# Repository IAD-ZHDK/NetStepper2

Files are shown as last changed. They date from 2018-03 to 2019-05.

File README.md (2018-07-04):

# NetStepper2
A networked stepper motor controller based on the ESP-WROOM-32 and the L6470. Examples built with netStepper can be seen in this [video](https://vimeo.com/278343342).  
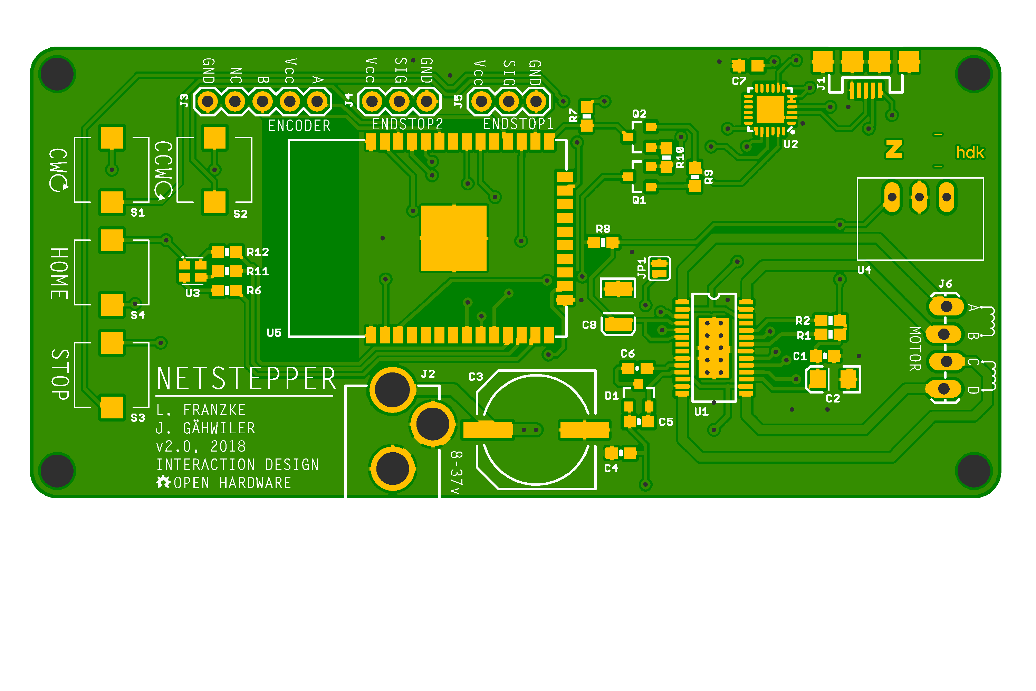
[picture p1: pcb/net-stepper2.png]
Board

## Parts

### Controllers

- Stepper Controller: `L6470` ([Datasheet](https://www.mouser.com/ds/2/389/l6470-954753.pdf), [Mouser](https://www.mouser.ch/ProductDetail/STMicroelectronics/L6470H?qs=sGAEpiMZZMuP%2fQeRSdvksPGSQkvtk%2fGb))
- SoC: `ESP-WROOM-32` ([Datasheet](https://espressif.com/sites/default/files/documentation/esp-wroom-32_datasheet_en.pdf), [Mouser](https://www.mouser.ch/ProductDetail/Adafruit/3320?qs=%2fha2pyFaduhvAZY8Ie1SD0odCwfSxZwX5aiqddL%252ba6k%3d))
- USB/UART: `CP2104` ([Datasheet](https://www.mouser.com/ds/2/368/cp2104-37496.pdf), [Mouser](https://www.mouser.ch/ProductDetail/Silicon-Labs/CP2104-F03-GMR?qs=sGAEpiMZZMtXqW1IUNX6MBk8lKhQ2c4Y))

### Interface

- RGB LED: `CLMVB-FKA-CFHEHLCBB7a363` ([Datasheet](https://www.mouser.com/ds/2/90/CLMVBFKA-276021.pdf), [Mouser](https://www.mouser.ch/ProductDetail/Cree-Inc/CLMVB-FKA-CFHEHLCBB7a363/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))
- Micro USB: `ZX62-B-5PA(33)` ([Datasheet](https://www.mouser.com/ds/2/185/ZX_catalog-939768.pdf), [Mouser](https://www.mouser.ch/ProductDetail/Hirose-Connector/ZX62-B-5PA33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))

### Other

- NPN Transistor: `MMBT2222` ([Datasheet](https://www.mouser.com/ds/2/308/MMBT2222LT1-D-80103.pdf), [Mouser](https://www.mouser.ch/ProductDetail/863-SMMBT2222ALT3G?r=863-SMMBT2222ALT3G))
- Double Diodes: `BAV99` ([Datasheet](https://www.mouser.com/ds/2/308/BAV99-1118535.pdf), [Mouser](https://www.mouser.ch/ProductDetail/ON-Semiconductor-Fairchild/BAV99?qs=sGAEpiMZZMudZehw8RjeZe6BnmRwGdH1))
- Traco: `TSR 1-2433`: ([Datasheet](https://www.mouser.com/ds/2/687/tsr1-537631.pdf), [Mouser](https://www.mouser.ch/ProductDetail/TRACO-Power/TSR-1-2433?qs=sGAEpiMZZMsF1ODjcwEocIuESINJH25XntreftV5zWI%3d))
- Button: `B3AL1002P-MS`: ([Datasheet](https://www.mouser.com/ds/2/307/en-b3al-6968.pdf), [Mouser](https://www.mouser.ch/ProductDetail/Omron-Electronics/B3AL-1002P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))
- Power Jack: `PTH-Lock`: ([Datasheet](https://www.sparkfun.com/datasheets/Prototyping/Barrel-Connector-PJ-202A.pdf), [Mouser](https://www.mouser.ch/ProductDetail/SparkFun/PRT-00119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))
- Tantalum Capacitor: `10uF`: ([Datasheet](https://www.mouser.com/ds/2/40/f93-776559.pdf), [Mouser](https://www.mouser.ch/ProductDetail/AVX/F931D106MAA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))
- Tantalum Capacitor: `47uF`: ([Datasheet](https://www.mouser.com/ds/2/40/f93-776559.pdf), [Mouser](https://www.mouser.ch/ProductDetail/AVX/F931A476KBA?qs=sGAEpiMZZMuEN2agSAc2puC4lhRhLeolV5NgMLhJRWs%3d))
- Electrolyte Capacitor: `100uF`: ([Datasheet](https://www.mouser.com/ds/2/88/SML%20series-552997.pdf), [Mouser](https://www.mouser.ch/ProductDetail/Illinois-Capacitor-CDE/107SML063M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))

## Notes

- ESP32 from Adafruit do not come in a tape/reel.

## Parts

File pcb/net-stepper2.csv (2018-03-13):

Part | Quantity | Value | Device | Package | Description | Place | Provided | Distributor | Ordernumber | Weblink | Remarks
C1 | 1 | 0.1uF | CAP0603-CAP (10V-10%) | 0603-CAP | 0.1uF ceramic capacitor | Yes | No | R2
C2 | 1 | 10uF | 10UF-TANT (10V-10%) | EIA3216 | 10uF Tantalum capacitor | Yes | No | Mouser | 647-F931D106MAA | https://www.mouser.ch/ProductDetail/AVX/F931D106MAA
C3 | 1 | 100uF | 100UF-63V-20%(ELECT) | NIC_10X10.5_CAP | 100uF 10x10.5mm capacitor | Yes | No | Mouser | 598-107SML063M | https://www.mouser.ch/ProductDetail/Illinois-Capacitor-CDE/107SML063M
C4, C5 | 2 | 0.22uF | CAP0603-CAP (50V-10%) | 0603-CAP | 0.22uF ceramic capacitor | Yes | No | R2
C6 | 1 | 10nF | 10NF/10000PF-50V-10%(0603) | 0603-CAP | 10nF ceramic capacitor | Yes | No | R2
C7 | 1 | 10uF | 10UF-0603-10V-10% | 603 | 10.0µF ceramic capacitors | Yes | No | R2
C8 | 1 | 47uF | 47UF-TANT-10V-10% | EIA3528 | 47uF tantalum capacitor | Yes | No | Mouser | 647-F931A476KBA | https://www.mouser.ch/ProductDetail/AVX/F931A476KBA?qs=sGAEpiMZZMuEN2agSAc2puC4lhRhLeolV5NgMLhJRWs%3d
R1, R2, R7, R8, R9, R10 | 6 | 10k | RESISTOR0603-RES-1/10W-1% | 0603-RES | 10k resistor | Yes | No | R2
R6, R11, R12 | 3 | 1k | RESISTOR0603-RES-1/10W-1% | 0603-RES | 1k resistor | Yes | No | R2
Q1, Q2 | 2 | 600mA/40V | TRANS_NPN-MMBT2222AL | SOT23-3 | NPN transistor | Yes | No | Mouser | 863-SMMBT2222ALT3G | https://www.mouser.ch/ProductDetail/863-SMMBT2222ALT3G?r=863-SMMBT2222ALT3G
D1 | 1 | BAV99 | BAV99 | SOT23-3@1 | Two small signal silicon diodes connected anode to cathode | Yes | No | Mouser | 512-BAV99 | https://www.mouser.ch/ProductDetail/ON-Semiconductor-Fairchild/BAV99?qs=sGAEpiMZZMudZehw8RjeZe6BnmRwGdH1
U1 | 1 | L6470 | L6470 | HTSSOP28 | 3A RMS/7A peak bipolar stepper motor driver with SPI control | Yes | No | Mouser | 511-L6470H | https://www.mouser.ch/ProductDetail/STMicroelectronics/L6470H?qs=sGAEpiMZZMuP%2fQeRSdvksPGSQkvtk%2fGb
U2 | 1 | CP2104 | CP2104 | QFN24_4MM_SMSC | USB to UART Bridge | Yes | No | Mouser | 634-CP2104-F03-GMR | https://www.mouser.ch/ProductDetail/Silicon-Labs/CP2104-F03-GMR?qs=sGAEpiMZZMtXqW1IUNX6MBk8lKhQ2c4Y
U3 | 1 | RGB-LED | RGB-LED-CLMVB-FKARGB | PLCC4-2MM-RGB | RGB LED 2mm x 2mm | Yes | No | Mouser | 941-CLMVBFKACFHEHLCB | https://www.mouser.ch/ProductDetail/Cree-Inc/CLMVB-FKA-CFHEHLCBB7a363/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
U4 | 1 | TRACO12433 | TRACO12433 | TRACO12433 | Voltage Regulator | No | No | Mouser | 495-TSR-1-2433 | https://www.mouser.ch/ProductDetail/TRACO-Power/TSR-1-2433?qs=sGAEpiMZZMsF1ODjcwEocIuESINJH25XntreftV5zWI%3d
U5 | 1 | ESP-WROOM-32 | ESP-WROOM-32 | ESP-WROOM-32 | ESP32 BLE & WiFi Module | Yes | Yes | Mouser | 485-3320 | https://www.mouser.ch/ProductDetail/Adafruit/3320 | Leider ist der Gurt geschnitten und die Module nun einzeln.
S1, S2, S3, S4 | 4 | B3AL-1002P-MS | B3AL-1002P-MS | B3AL-1002P-MS | Button | Yes | No | Mouser | 653-B3AL-1002P | https://www.mouser.ch/ProductDetail/Omron-Electronics/B3AL-1002P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
J1 | 1 | MICRO-USB | USB_MICRO-B_SMT | USB-MICROB | USB Type Micro-B Connector | Yes | No | Mouser | 798-ZX62-B-5PA33 | https://www.mouser.ch/ProductDetail/Hirose-Connector/ZX62-B-5PA33
J2 | 1 | POWER_JACKPTH_LOCK | POWER_JACKPTH_LOCK | POWER_JACK_PTH_LOCK | Power Jack | No | No | Mouser | 474-PRT-00119 | https://www.mouser.ch/ProductDetail/SparkFun/PRT-00119
J3 | 1 | ENCODER | CONN_05 | 1X05 | Multi connection point | No | No
J4 | 1 | ENDSTOP2 | CONN_03 | 1X03 | Multi connection point | No | No
J5 | 1 | ENDSTOP1 | CONN_03 | 1X03 | Multi connection point | No | No
J6 | 1 | STEPER | CONN_04 | 1X04 | Multi connection point | No | No

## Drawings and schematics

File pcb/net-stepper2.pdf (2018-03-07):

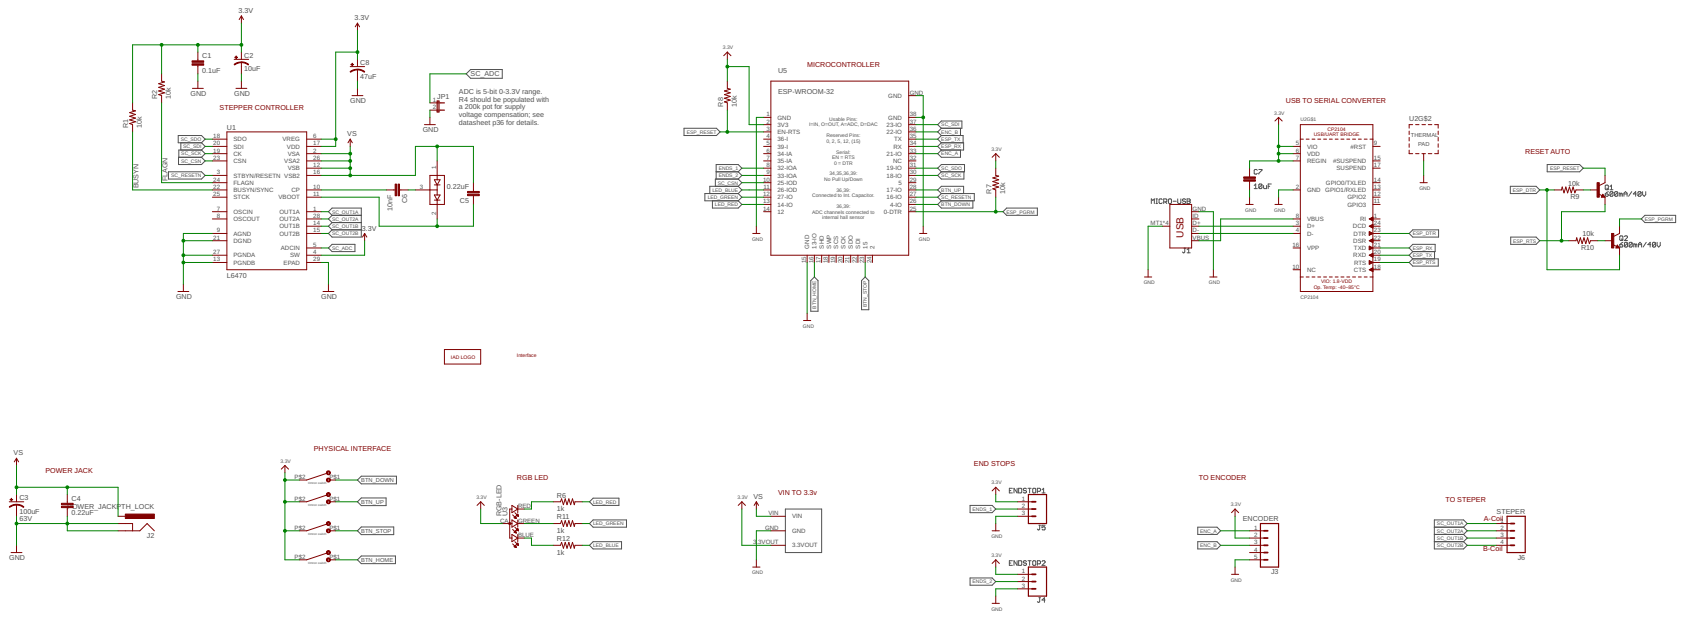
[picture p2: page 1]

ADC is 5-bit 0-3.3V range. R4 should be populated with
a 200k pot for supply
voltage compensation; see

USB TO SERIAL CONVERTER

I=IN, O=OUT, A=ADC, D=DAC
Reserved Pins: 0, 2, 5, 12, (15) Serial: EN = RTS

0 = DTR
34,35,36,39: No Pull Up/Down

36,39: Connected to Int. Capacitor. 36,39: ADC channels connected to

VIO: 1.8-VDD Op. Temp: -40~85°C

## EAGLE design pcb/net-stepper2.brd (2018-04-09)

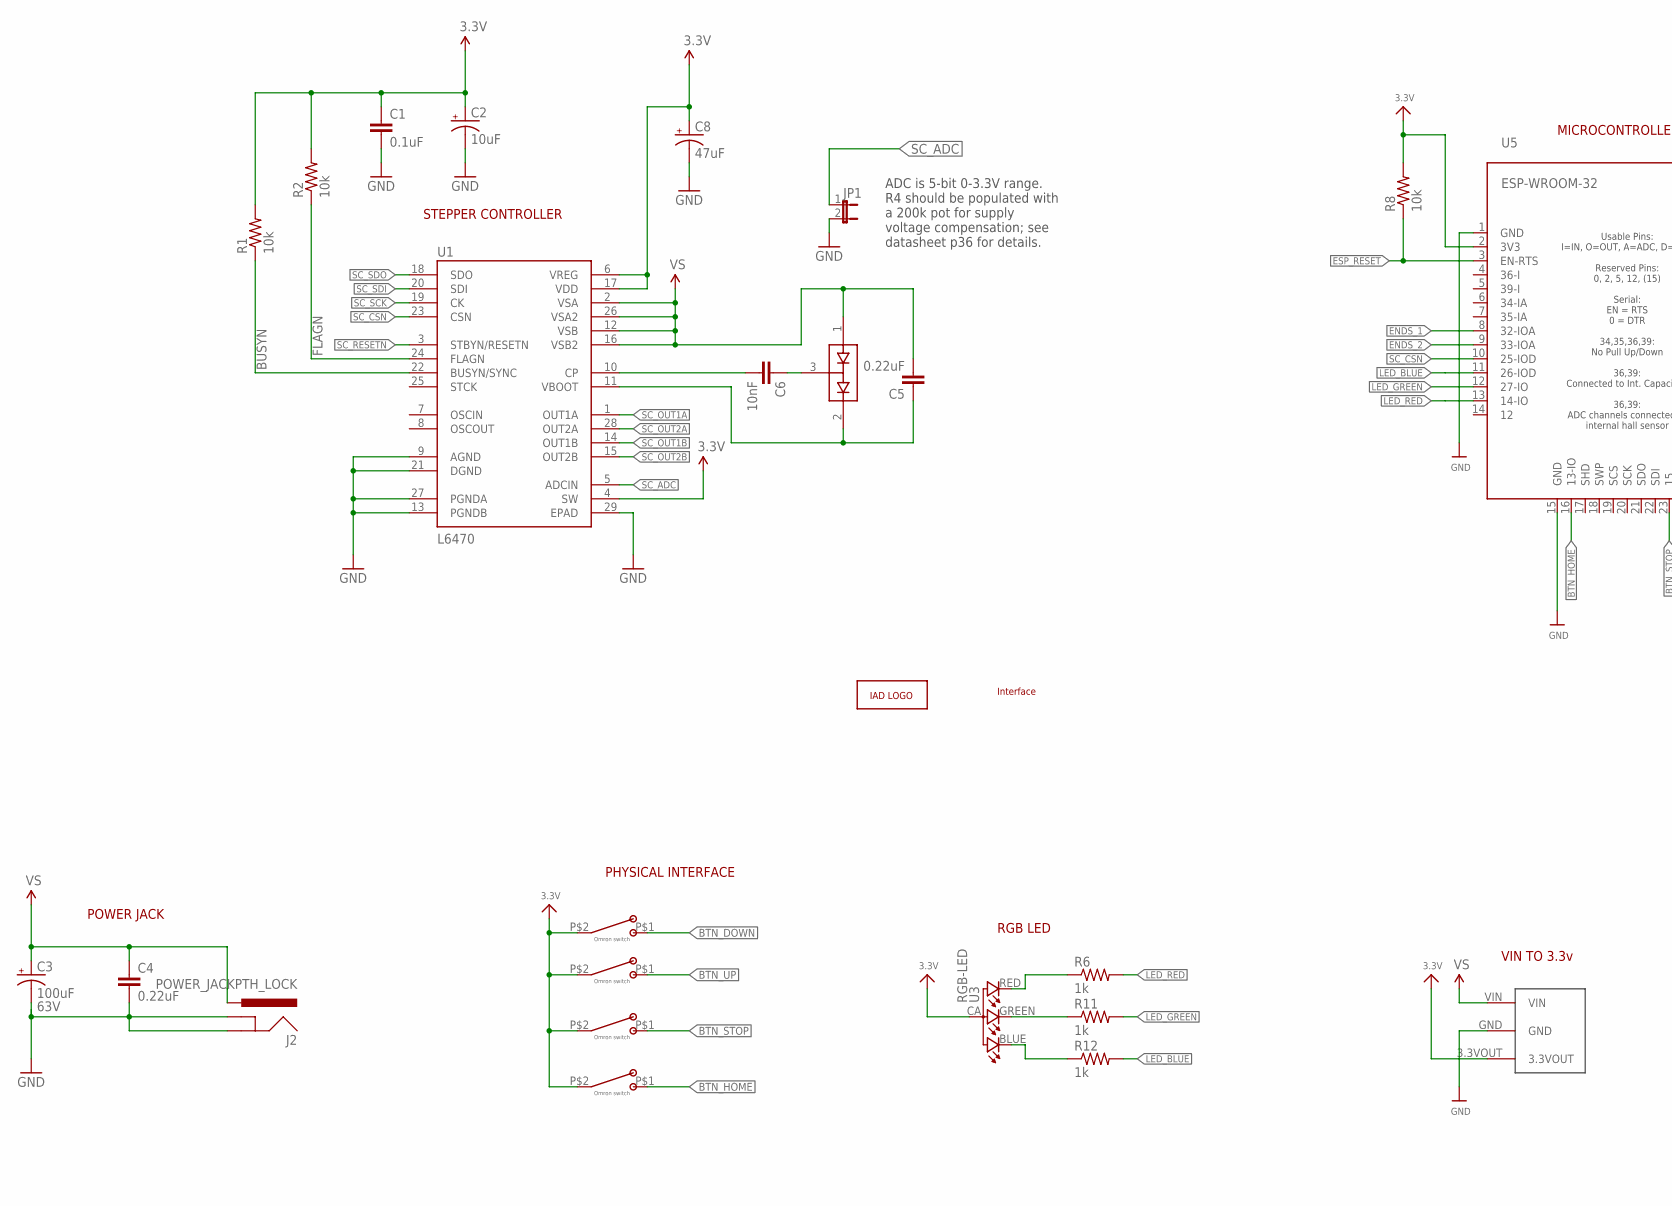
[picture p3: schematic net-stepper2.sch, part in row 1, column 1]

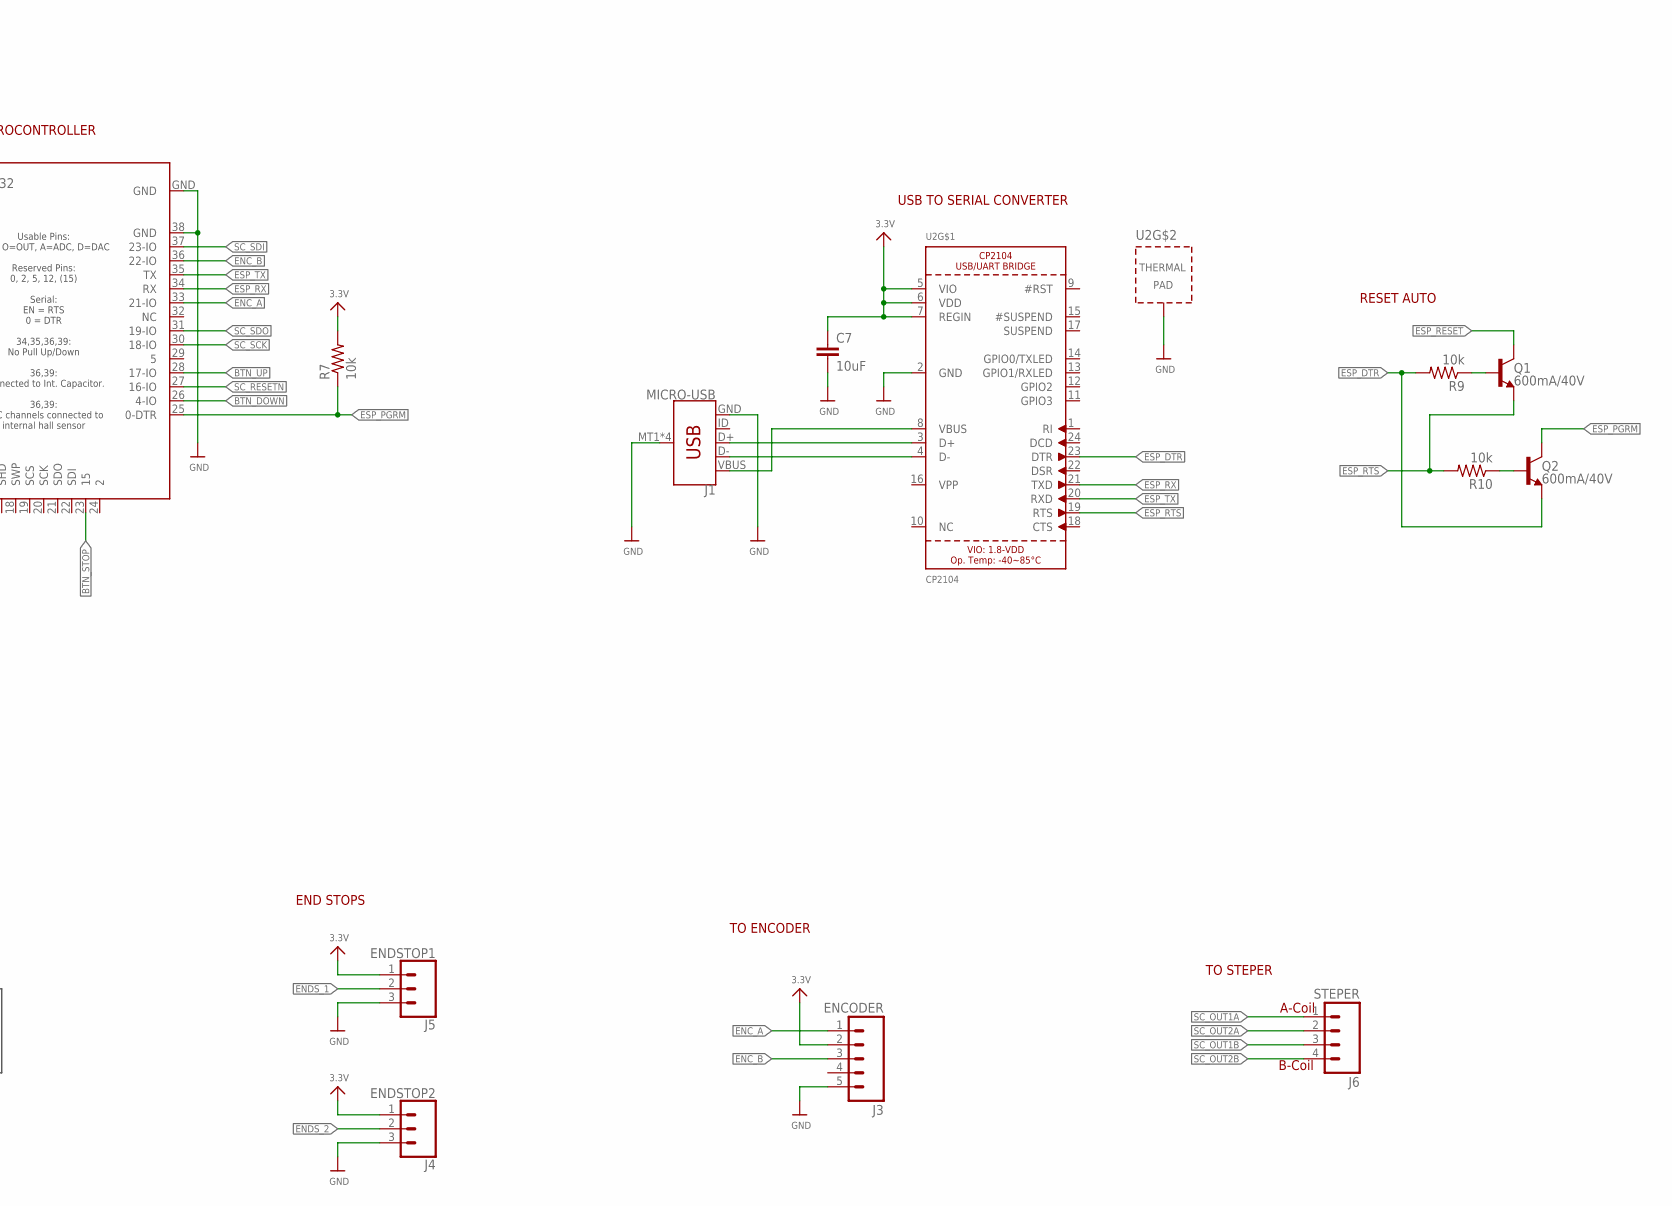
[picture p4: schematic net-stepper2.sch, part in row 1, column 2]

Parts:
A1: ZHDK_LOGO_METAL; ZHDK_LOGO
A2: INTERFACE_NETSTEPPER
C1: 0.1uF; 0603-CAP
C2: 10uF; EIA3216
C3: 100uF; NIC_10X10.5_CAP
C4, C5: 0.22uF; 0603-CAP
C6: 10nF; 0603-CAP
C7: 10uF; 0603
C8: 47uF; EIA3528
D1: BAV99; SOT23-3@1
J1: MICRO-USB; USB-MICROB
J2: POWER_JACKPTH_LOCK; POWER_JACK_PTH_LOCK
J3: ENCODER; 1X05
J4: ENDSTOP2; 1X03
J5: ENDSTOP1; 1X03
J6: STEPER; 1X04_LOCK_LONGPADS
JP1: JUMPER-2SMD-NC; SJ_2S
Q1, Q2: 600mA/40V; SOT23-3
R1, R2, R7, R8, R9, R10: 10k; 0603-RES
R6, R11, R12: 1k; 0603-RES
S1, S2, S3, S4: B3AL-1002P-MS
U1: L6470; HTSSOP28
U2: CP2104; QFN24_4MM_SMSC
U3: RGB-LED; PLCC4-2MM-RGB
U4: TRACO12433
U5: ESP-WROOM-32

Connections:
3.3V: C1.1, C2.A (+), C7.1, C8.A (+), J3.2, J4.1, J5.1, R1.2, R2.2, R7.2, R8.2, S1.P$2, S2.P$2, S3.P$2, S4.P$2, U1.4 (SW), U1.6 (VREG), U1.17 (VDD), U2.5 (VIO), U2.6 (VDD), U2.7 (REGIN), U3.CA (1), U4.3.3VOUT, U5.2 (3V3)
BTN_DOWN: S1.P$1, U5.26 (4-IO)
BTN_HOME: S4.P$1, U5.16 (13-IO)
BTN_STOP: S3.P$1, U5.23 (15)
BTN_UP: S2.P$1, U5.28 (17-IO)
BUSYN: R1.1, U1.22 (BUSYN/SYNC)
CP_HIGH: C6.1, D1.3 (COM)
ENC_A: J3.1, U5.33 (21-IO)
ENC_B: J3.3, U5.36 (22-IO)
ENDS_1: J5.2, U5.8 (32-IOA)
ENDS_2: J4.2, U5.9 (33-IOA)
ESP_DTR: Q2.2 (E), R9.2, U2.23 (DTR)
ESP_PGRM: Q2.3 (C), R7.1, U5.25 (0-DTR)
ESP_RESET: Q1.3 (C), R8.1, U5.3 (EN-RTS)
ESP_RTS: Q1.2 (E), R10.2, U2.19 (RTS)
ESP_RX: U2.21 (TXD), U5.34 (RX)
ESP_TX: U2.20 (RXD), U5.35 (TX)
FLAGN: R2.1, U1.24 (FLAGN)
GND: C1.2, C2.C (-), C3.-, C4.2, C7.2, C8.C (-), J1.GND, J1.MT1 (SHIELD), J1.MT2 (SHIELD), J1.P$1 (SHIELD), J1.P$2 (SHIELD), J2.GND, J2.GNDBREAK, J3.5, J4.3, J5.3, JP1.2, U1.9 (AGND), U1.13 (PGNDB), U1.21 (DGND), U1.27 (PGNDA), U1.29 (EPAD), U2.2 (GND), U2.THERM (TP), U4.GND, U5.1 (GND), U5.15 (GND), U5.38 (GND), U5.GND
LED_BLUE: R12.2, U5.11 (26-IOD)
LED_GREEN: R11.2, U5.12 (27-IO)
LED_RED: R6.2, U5.13 (14-IO)
unnamed: J1.VBUS, U2.8 (VBUS)
unnamed: R11.1, U3.GREEN (3)
unnamed: R6.1, U3.RED (4)
unnamed: J1.D+, U2.3 (D+)
unnamed: J1.D-, U2.4 (D-)
unnamed: R12.1, U3.BLUE (2)
unnamed: Q1.1 (B), R9.1
unnamed: Q2.1 (B), R10.1
SC_ADC: JP1.1, U1.5 (ADCIN)
SC_CSN: U1.23 (CSN), U5.10 (25-IOD)
SC_OUT1A: J6.1, U1.1 (OUT1A)
SC_OUT1B: J6.3, U1.14 (OUT1B)
SC_OUT2A: J6.2, U1.28 (OUT2A)
SC_OUT2B: J6.4, U1.15 (OUT2B)
SC_RESETN: U1.3 (STBYN/RESETN), U5.27 (16-IO)
SC_SCK: U1.19 (CK), U5.30 (18-IO)
SC_SDI: U1.20 (SDI), U5.37 (23-IO)
SC_SDO: U1.18 (SDO), U5.31 (19-IO)
VS: C3.+, C4.1, C5.2, D1.1 (A1), J2.PWR, U1.2 (VSA), U1.12 (VSB), U1.16 (VSB2), U1.26 (VSA2), U4.VIN
V_BOOT: C5.1, D1.2 (C2), U1.11 (VBOOT)
V_CP: C6.2, U1.10 (CP)

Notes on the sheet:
63V
B-Coil
A-Coil
ADC is 5-bit 0-3.3V range. R4 should be populated with a 200k pot for supply voltage compensation; see datasheet p36 for details.
MICROCONTROLLER
RESET AUTO
END STOPS
VIN TO 3.3v
TO ENCODER
PHYSICAL INTERFACE
TO STEPER
POWER JACK
STEPPER CONTROLLER
USB TO SERIAL CONVERTER
RGB LED

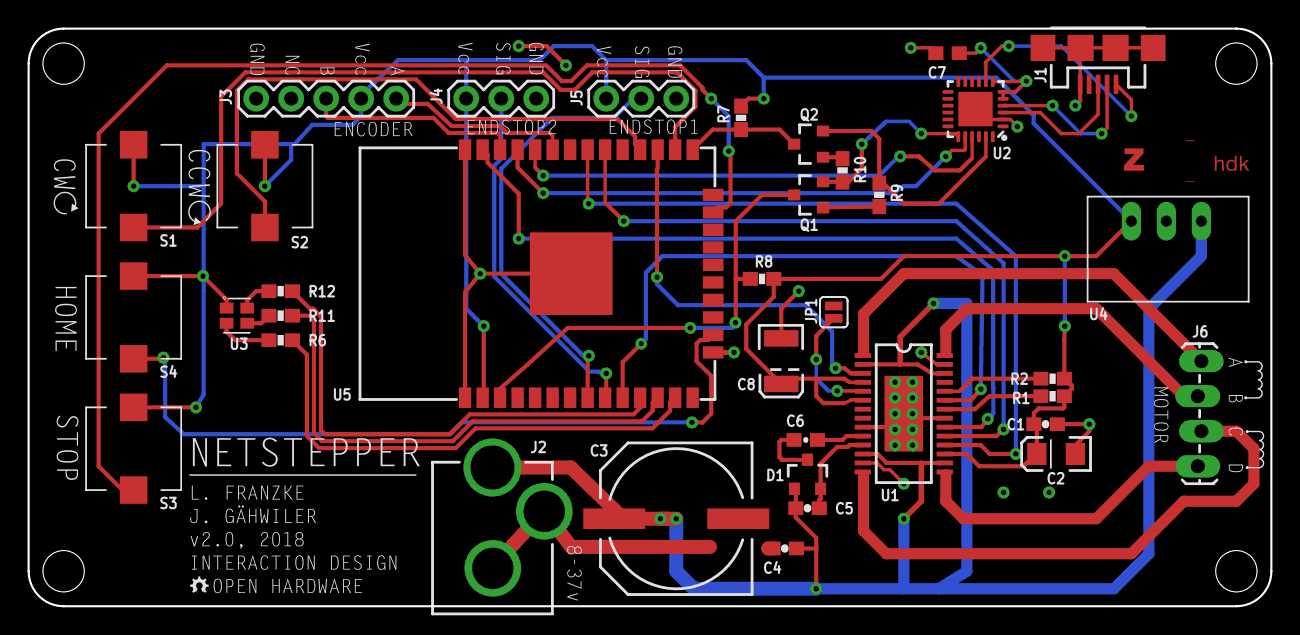
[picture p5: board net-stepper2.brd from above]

Board: 2 copper layers, 90.2 x 41.9 mm, 38 parts (0 on the bottom side), 43 nets.

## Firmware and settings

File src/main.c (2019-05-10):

#include <art32/numbers.h>
#include <art32/smooth.h>
#include <art32/strconv.h>
#include <driver/adc.h>
#include <driver/gpio.h>
#include <naos.h>
#include <string.h>

#include "buttons.h"
#include "encoder.h"
#include "end_stop.h"
#include "l6470.h"
#include "led.h"
#include "sharp.h"

static naos_status_t current_status = NAOS_DISCONNECTED;

int32_t micro_steps = 128;
double gear_ratio = 0;
int32_t resolution = 0;
double max_speed = 0;
double acceleration = 0;
double deceleration = 0;
double min_target = 0;
double max_target = 0;
bool use_sensor_1 = false;
bool use_sensor_2 = false;
bool convert_sharp = false;

a32_smooth_t *sensor_smooth_1;
a32_smooth_t *sensor_smooth_2;

bool blocked = true;

static void set_status() {
  // set led accordingly
  switch (current_status) {
    case NAOS_DISCONNECTED:
      led_set(1024, 0, 0);
      break;
    case NAOS_CONNECTED:
      led_set(0, 0, 1024);
      break;
    case NAOS_NETWORKED:
      if (blocked) {
        led_set(1024, 1024, 0);
      } else {
        led_set(0, 1024, 0);
      }
      break;
  }
}

static void status(naos_status_t status) {
  // set last status
  current_status = status;

  // set new status
  set_status();
}

static void ping() {
  // blink white once
  led_set(1024, 1024, 1024);
  naos_delay(300);

  // set status
  set_status();
}

static void online() {
  // subscribe to topics
  naos_subscribe("forward", 0, NAOS_LOCAL);
  naos_subscribe("backward", 0, NAOS_LOCAL);
  naos_subscribe("target", 0, NAOS_LOCAL);
  naos_subscribe("stop", 0, NAOS_LOCAL);
  naos_subscribe("reset", 0, NAOS_LOCAL);
  naos_subscribe("home", 0, NAOS_LOCAL);
}

static void update(const char *param, const char *value) {
  // handle "micro-steps"
  if (strcmp(param, "micro-steps") == 0) {
    // make motor stop (remove power)
    l6470_hard_hiz();

    // set setting
    micro_steps = l6470_set_step_mode_int(naos_get_l("micro-steps"));

    // set corrected value
    naos_set_l("micro-steps", micro_steps);

    // reset position
    l6470_reset_position();
  }

  // handle "max-speed"
  if (strcmp(param, "max-speed") == 0) {
    // constrain value
    max_speed = naos_get_d("max-speed");

    // set constrained value
    naos_set_d("max-speed", max_speed);

    // set setting
    l6470_set_maximum_speed(l6470_calculate_maximum_speed(max_speed));

    // set full step mode to two times max speed (no full stepping)
    l6470_set_full_step_speed(l6470_calculate_full_step_speed(max_speed * 2));
  }

  // handle "acceleration"
  if (strcmp(param, "acceleration") == 0) {
    // constrain value
    acceleration = naos_get_d("acceleration");

    // set constrained value
    naos_set_d("acceleration", acceleration);

    // set setting
    l6470_set_acceleration(l6470_calculate_acceleration(acceleration));
  }

  // handle "deceleration"
  if (strcmp(param, "deceleration") == 0) {
    // constrain value
    deceleration = naos_get_d("deceleration");

    // set constrained value
    naos_set_d("deceleration", deceleration);

    // set setting
    l6470_set_deceleration(l6470_calculate_deceleration(deceleration));
  }
}

static void message(const char *topic, uint8_t *payload, size_t len, naos_scope_t scope) {
  // immediately return if blocked
  if (blocked) {
    return;
  }

  // make string
  char *str = (char *)payload;

  // handle "forward" command
  if (strcmp(topic, "forward") == 0 && scope == NAOS_LOCAL) {
    // run forward
    l6470_run(L6470_FORWARD, l6470_calculate_speed(max_speed));
  }

  // handle "backward command
  if (strcmp(topic, "backward") == 0 && scope == NAOS_LOCAL) {
    // run backward
    l6470_run(L6470_REVERSE, l6470_calculate_speed(max_speed));
  }

  // handle "target" command
  if (strcmp(topic, "target") == 0 && scope == NAOS_LOCAL) {
    // calculate position factor
    double steps_per_rev = micro_steps * resolution * gear_ratio;

    // calculate minimum and maximum physical position
    double min_phys_target = L6470_I22_MIN / steps_per_rev;
    double max_phys_target = L6470_I22_MAX / steps_per_rev;

    // get target
    double target = a32_str2d(str);

    // constrain target
    target = a32_constrain_d(target, min_phys_target, max_phys_target);
    target = a32_constrain_d(target, min_target, max_target);

    // calculate real position
    int32_t pos = (int32_t)(target * steps_per_rev);

    // constrain position
    pos = a32_constrain_l(pos, L6470_I22_MIN, L6470_I22_MAX);

    // approach target
    l6470_approach_target(pos);
  }

  // handle "stop" command
  if (strcmp(topic, "stop") == 0 && scope == NAOS_LOCAL) {
    // stop motor
    l6470_soft_stop();
  }

  // handle "reset" command
  if (strcmp(topic, "reset") == 0 && scope == NAOS_LOCAL) {
    // reset position
    l6470_reset_position();
  }

  // handle "home" command
  if (strcmp(topic, "home") == 0 && scope == NAOS_LOCAL) {
    // approach home
    l6470_approach_home();
  }
}

static void loop() {
  // this loop is called at a rate of 100/s

  // get time
  uint32_t now = naos_millis();

  // check sensor 1
  if (use_sensor_1) {
    // prepare counter
    static uint32_t last_send_1 = 0;

    // read sensor
    double es1 = end_stop_read_1();

    // convert value if requested
    if (convert_sharp) {
      es1 = sharp_convert(es1);
    }

    // smooth value
    es1 = a32_smooth_update(sensor_smooth_1, es1);

    // check if 100ms passed
    if (last_send_1 + 100 < now) {
      // set time
      last_send_1 = now;

      // publish sensor value
      naos_publish_d("sensor1", es1, 0, false, NAOS_LOCAL);
    }
  }

  // check sensor 2
  if (use_sensor_2) {
    // prepare counter
    static uint32_t last_send_2 = 0;

    // read sensors
    double es2 = end_stop_read_2();

    // convert value if requested
    if (convert_sharp) {
      es2 = sharp_convert(es2);
    }

    // smooth value
    es2 = a32_smooth_update(sensor_smooth_2, es2);

    // check if 100ms passed
    if (last_send_2 + 100 < now) {
      // set time
      last_send_2 = now;

      // publish sensor value
      naos_publish_d("sensor2", es2, 0, false, NAOS_LOCAL);
    }
  }
}

static void press(buttons_type_t type, bool pressed) {
  // prepare home press counter
  static uint32_t home_press = 0;
  static uint32_t stop_press = 0;

  // turn forward if cw is released
  if (type == BUTTONS_TYPE_CW && !pressed) {
    // run forward
    l6470_run(L6470_FORWARD, l6470_calculate_speed(max_speed));
  }

  // turn backwards if ccw is released
  if (type == BUTTONS_TYPE_CCW && !pressed) {
    // run backward
    l6470_run(L6470_REVERSE, l6470_calculate_speed(max_speed));
  }

  // stop motor and block if stop is pressed
  if (type == BUTTONS_TYPE_STOP && pressed) {
    // stop motor
    l6470_soft_stop();

    // set stop flag
    blocked = true;
    set_status();

    // save time
    stop_press = naos_millis();
  }

  // handle stop button release
  if (type == BUTTONS_TYPE_STOP && !pressed) {
    // get time difference
    uint32_t diff = naos_millis() - stop_press;

    // reset blocked flag if button has been released quickly
    if (diff < 500) {
      // set flag
      blocked = false;
      set_status();

      return;
    }

    // otherwise keep blocked flag set
  }

  // set time if pressed
  if (type == BUTTONS_TYPE_HOME && pressed) {
    home_press = naos_millis();
  }

  // handle home button release
  if (type == BUTTONS_TYPE_HOME && !pressed) {
    // get time difference
    uint32_t diff = naos_millis() - home_press;

    // approach home if buttons has been released quickly
    if (diff < 500) {
      // approach home
      l6470_approach_home();

      return;
    }

    // otherwise reset position and stop

    // set home pos
    l6470_reset_position();

    // stop motor
    l6470_soft_stop();

    // flash led
    led_set(255, 255, 255);
    naos_delay(300);
    set_status();
  }
}

static void position(double p) {}

static void end_stop(end_stop_pin_t pin, bool on) {}

static void offline() {
  // stop motor
  l6470_soft_stop();
}

static naos_param_t params[] = {
    {.name = "micro-steps", .type = NAOS_LONG, .default_l = 128},
    {.name = "gear-ratio", .type = NAOS_DOUBLE, .default_d = 5.18, .sync_d = &gear_ratio},
    {.name = "resolution", .type = NAOS_LONG, .default_l = 200, .sync_l = &resolution},
    {.name = "max-speed", .type = NAOS_DOUBLE, .default_d = 900},
    {.name = "acceleration", .type = NAOS_DOUBLE, .default_d = 900},
    {.name = "deceleration", .type = NAOS_DOUBLE, .default_d = 900},
    {.name = "min-target", .type = NAOS_DOUBLE, .default_d = -5, .sync_d = &min_target},
    {.name = "max-target", .type = NAOS_DOUBLE, .default_d = 5, .sync_d = &max_target},
    {.name = "use-sensor-1", .type = NAOS_BOOL, .default_b = false, .sync_b = &use_sensor_1},
    {.name = "use-sensor-2", .type = NAOS_BOOL, .default_b = false, .sync_b = &use_sensor_2},
    {.name = "convert-sharp", .type = NAOS_BOOL, .default_b = false, .sync_b = &convert_sharp},
};

static naos_config_t config = {
    .device_type = "NetStepper2",
    .firmware_version = "0.5.0",
    .parameters = params,
    .num_parameters = 11,
    .ping_callback = ping,
    .status_callback = status,
    .online_callback = online,
    .update_callback = update,
    .message_callback = message,
    .loop_callback = loop,
    .loop_interval = 10,
    .offline_callback = offline,
};

void app_main() {
  // install gpio interrupt service
  gpio_install_isr_service(0);

  // set adc capture width
  adc1_config_width(ADC_WIDTH_10Bit);

  // initialize led
  led_init();

  // initialize buttons
  buttons_init(press);

  // initialize encoder
  encoder_init(position);

  // initialize l6470
  l6470_init();

  // initialize sensors
  sensor_smooth_1 = a32_smooth_new(16);
  sensor_smooth_2 = a32_smooth_new(16);

  // initialize end stops
  end_stop_init(end_stop, true);

  // initialize naos
  naos_init(&config);

  // set step mode
  micro_steps = l6470_set_step_mode_int(naos_get_l("micro-steps"));

  // get speeds
  max_speed = naos_get_d("max-speed");
  acceleration = naos_get_d("acceleration");
  deceleration = naos_get_d("deceleration");

  // reset minimum speed
  l6470_set_minimum_speed(l6470_calculate_minimum_speed(0));

  // set initial speeds
  l6470_set_maximum_speed(l6470_calculate_maximum_speed(max_speed));
  l6470_set_acceleration(l6470_calculate_acceleration(acceleration));
  l6470_set_deceleration(l6470_calculate_deceleration(deceleration));

  // set full step mode to two times max speed (no full stepping)
  l6470_set_full_step_speed(l6470_calculate_full_step_speed(max_speed * 2));
}

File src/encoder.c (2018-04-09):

#include <driver/gpio.h>
#include <freertos/FreeRTOS.h>
#include <freertos/queue.h>
#include <freertos/task.h>

#include "encoder.h"

// https://github.com/PaulStoffregen/Encoder/blob/master/Encoder.h

#define ENCODER_A_SEL GPIO_SEL_22
#define ENCODER_B_SEL GPIO_SEL_21

#define ENCODER_A_NUM GPIO_NUM_22
#define ENCODER_B_NUM GPIO_NUM_21

#define ENCODER_RESOLUTION 400
#define ENCODER_ACCURACY 40

static encoder_handler_t encoder_handler;

static volatile uint8_t encoder_state = 0;
static volatile int32_t encoder_total = 0;
static volatile int32_t encoder_last = 0;

static QueueHandle_t encoder_queue;

static void encoder_isr(void *_) {
  // read pins
  int a = gpio_get_level(ENCODER_A_NUM);
  int b = gpio_get_level(ENCODER_B_NUM);

  // calculate encoder change
  uint8_t state = (uint8_t)(encoder_state & 3);
  if (a) state |= 4;
  if (b) state |= 8;

  // save new state
  encoder_state = (state >> 2);

  // save relative change
  switch (state) {
    case 1:
    case 7:
    case 8:
    case 14: {
      encoder_total += 1;
      break;
    }
    case 2:
    case 4:
    case 11:
    case 13: {
      encoder_total -= 1;
      break;
    }
    case 3:
    case 12: {
      encoder_total += 2;
      break;
    }
    case 6:
    case 9: {
      encoder_total -= 2;
      break;
    }
    default: {
      // no movement
    }
  }

  // check if an update is due
  int32_t diff = ENCODER_RESOLUTION / ENCODER_ACCURACY;
  if (encoder_total > encoder_last + diff || encoder_total < encoder_last - diff) {
    // remember value
    encoder_last = encoder_total;

    // send on queue
    xQueueSendFromISR(encoder_queue, (void *)&encoder_total, NULL);
  }
}

static void encoder_task(void *_) {
  // loop forever
  for (;;) {
    // get all button events
    int32_t n;
    while (xQueueReceive(encoder_queue, &n, portMAX_DELAY) == pdTRUE) {
      // calculate real position
      double pos = n;
      pos /= ENCODER_RESOLUTION;

      // call handler with position
      encoder_handler(pos);
    }
  }
}

void encoder_init(encoder_handler_t handler) {
  // set handler
  encoder_handler = handler;

  // create queue
  encoder_queue = xQueueCreate(16, sizeof(int32_t));

  // configure rotation pins
  gpio_config_t rc;
  rc.pin_bit_mask = ENCODER_A_SEL | ENCODER_B_SEL;
  rc.mode = GPIO_MODE_INPUT;
  rc.intr_type = GPIO_INTR_ANYEDGE;
  rc.pull_up_en = GPIO_PULLUP_ENABLE;
  rc.pull_down_en = GPIO_PULLDOWN_DISABLE;
  gpio_config(&rc);

  // preset state
  if (gpio_get_level(ENCODER_A_NUM)) encoder_state |= 1;
  if (gpio_get_level(ENCODER_B_NUM)) encoder_state |= 2;

  // add interrupt handlers
  gpio_isr_handler_add(ENCODER_A_NUM, encoder_isr, NULL);
  gpio_isr_handler_add(ENCODER_B_NUM, encoder_isr, NULL);

  // run task
  xTaskCreatePinnedToCore(encoder_task, "enc", 2048, NULL, 2, NULL, 1);
}

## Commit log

2018-01-30 implemented device status
2018-02-02 Board Layout and Schematic
    [ESP_L6470.brd, ESP_L6470.sch]
2018-02-27 Update schematic with USB to Serial
    [ESP_L6470.brd, ESP_L6470.sch]
2018-02-27 added some components
    [ESP_L6470.brd, ESP_L6470.sch]
2018-02-28 update with USB to Serial
    [ESP_L6470.brd, ESP_L6470.sch]
2018-03-02 Updated board
    [ESP_L6470.brd, ESP_L6470.sch]
2018-03-05 Updated with silkscreen
    [ESP_L6470.brd, ESP_L6470.sch]
2018-03-06 select all layers
    [ESP_L6470.brd]
2018-03-06 removed unused wire
    [ESP_L6470.brd]
2018-03-06 renamed some parts
    [ESP_L6470.brd, ESP_L6470.sch]
2018-03-06 approved some errors
    [ESP_L6470.sch]
2018-03-06 renamed aesthetics
    [ESP_L6470.brd, ESP_L6470.sch]
2018-03-06 fixed tx and rx pins and removed jumpers
    [ESP_L6470.brd, ESP_L6470.sch]
2018-03-06 moved pcb to sub directory
    [net-stepper2.brd, net-stepper2.sch]
2018-03-06 moved board
    [net-stepper2.brd]
2018-03-06 replaced esp32 component
    [net-stepper2.brd, net-stepper2.sch]
2018-03-06 removed unused signals
    [net-stepper2.brd, net-stepper2.sch]
2018-03-06 reorganized schematics
    [net-stepper2.brd, net-stepper2.sch]
2018-03-06 connect usb mounting pins to ground
    [net-stepper2.brd, net-stepper2.sch]
2018-03-06 changed pull resistors to 10k in order remove one resistor family
    [net-stepper2.brd, net-stepper2.sch]
2018-03-06 replaced cp2104 in order to connect the thermal pad to ground
    [net-stepper2.brd, net-stepper2.sch]
2018-03-06 updated schematics
    [net-stepper2.sch]
2018-03-06 added capacitor
    [net-stepper2.brd, net-stepper2.sch]
2018-03-06 removed not needed ground plan vertices
    [net-stepper2.brd]
2018-03-06 remapped pins
    [net-stepper2.brd, net-stepper2.sch]
2018-03-06 prepared new routing
    [net-stepper2.brd, net-stepper2.sch]
2018-03-06 Missing routing fixed
    [net-stepper2.brd, net-stepper2.sch]
2018-03-07 added top ground plate
    [net-stepper2.brd]
2018-03-07 rotated layout
    [net-stepper2.brd]
2018-03-07 smashed comoponents and placed names
    [net-stepper2.brd]
2018-03-07 removed todo
    [net-stepper2.sch]
2018-03-07 approved error
    [net-stepper2.sch]
2018-03-07 set via sizes and updated design rules to comply
    [net-stepper2.brd]
2018-03-07 added missing name label
    [net-stepper2.brd]
2018-03-07 added schematic pdf
2018-03-07 added bom and updated readme
    [net-stepper2.csv]
2018-03-07 Last check
    [net-stepper2.brd, net-stepper2.sch]
2018-03-07 updated label
    [net-stepper2.brd]
2018-03-07 removec r5 from bom
    [net-stepper2.csv]
2018-03-07 updated bom
    [net-stepper2.csv]
2018-03-07 Drill size change
    [net-stepper2.brd]
2018-03-07 updated exports
    [net-stepper2.brd]
2018-03-21 stop motor when going offline
2018-03-21 implemented async button handling
2018-03-22 added encoder
2018-03-22 renamed enc to encoder
2018-03-22 changed case
2018-04-05 Fixed minor trace mistake
    [net-stepper2.brd]
2018-04-09 set new buttons
2018-04-09 added led control
2018-04-09 added todo
    [net-stepper2.sch]
2018-04-09 updated encoder pins
2018-04-09 updated chip select pin
2018-04-09 set led to yellow in blocked mode
2018-04-11 properly calculate real voltage
2019-04-18 added gear ratio parameter
2019-05-09 fix 22 bits clamping
    [l6470.c]
2019-05-09 fix usage of min and max
    [l6470.c]
2019-05-10 added led feedback for home position reset
    [main.c]

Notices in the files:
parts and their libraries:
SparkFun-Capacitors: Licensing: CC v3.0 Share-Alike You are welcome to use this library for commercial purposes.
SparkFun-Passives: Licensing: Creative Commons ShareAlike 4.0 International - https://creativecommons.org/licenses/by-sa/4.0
